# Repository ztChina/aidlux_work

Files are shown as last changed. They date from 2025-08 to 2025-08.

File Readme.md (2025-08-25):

## 目录
* [项目介绍](#项目介绍)
* [系统架构](#系统架构)
* [环境及依赖配置](#环境及依赖配置)
* [硬件配置](#硬件配置)
* [运行](#运行)

## 项目介绍
- 本项目基于思岚 RPLIDAR A1 激光雷达，使用 Gmapping 进行 2D SLAM 建图，并通过 ROS Navigation Stack 实现全局/局部规划与 AMCL 粒子滤波定位的自主导航。项目包含：
    - 雷达驱动与 TF 配置
    - Gmapping 参数优化与地图保存
    - AMCL 定位与导航（全局/局部路径规划）
    - YOLO 人体识别（融合视觉与雷达/里程计，支持跟随/到人）
    - 语音交互导航（语音设定目标点、启停、模式切换与状态播报）
    - 可即用的启动脚本与参数模板，帮助快速部署到实际机器人

## 系统架构


## 环境及依赖配置
- ROS相关环境配置及依赖安装见[相关文档](https://github.com/ztChina/aidlux_work/blob/main/ros_navigation/README.md)
- YOLO相关环境配置及依赖安装见[相关文档](https://github.com/ztChina/aidlux_work/blob/main/vision_part/README.md)
- 语音1交互相关环境配置及依赖安装见[相关文档](https://github.com/ztChina/aidlux_work/blob/main/AI_part/readme.md)
- 语音2交互功能相关环境配置及依赖安装见[相关文档](https://github.com/ztChina/aidlux_work/tree/main/Dialog-models-and-plugins)
- STM32相关环境配置与原理图见[相关文档](https://github.com/ztChina/aidlux_work/blob/main/%E5%B5%8C%E5%85%A5%E5%BC%8F%E9%83%A8%E5%88%86/readme.md)

## 硬件配置


[可查看 xlsx文件](https://github.com/ztChina/aidlux_work/raw/main/硬件清单.xlsx)

## 运行
### [ROS部分运行示例](https://github.com/ztChina/aidlux_work/blob/main/ros_navigation/README.md#%E5%90%AF%E5%8A%A8%E7%A4%BA%E4%BE%8B)
### [语音交互部分](https://github.com/ztChina/aidlux_work/blob/main/Dialog-models-and-plugins/README.md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)

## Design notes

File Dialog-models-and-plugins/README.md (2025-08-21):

# 目录
* [基本功能](#基本功能)
* [调试文档](#wukong语音交互调试文档)

# 基本功能
## 1.与`ROS`通信
```
pip install pyzmq
```
- `data_publisher.py`
- `ros_listener.py`

## 2.与`stm32`通信
```
pip install pyserial
```
- `get_stm32_msg.py`<br>
监听串口，一旦满足条件，则会发布到指定信息到socket本地6000端口。

## 3.功能：
### 1. `JustRun.py`：  <br>
接收跑路指令，并把消息发送给`ROS`，自动导航到指定地点。 <br>
### 2. `Water.py`： <br>
接收用户询问，返回湿度情况。
###  3. `get_stm32_msg.py`：<br>
接收`stm`串口通信，并在后台检测湿度变化，满足条件后唤醒，并输出语音，然后发消息给`ros`。
##### 3.1 `LifeCycleHandler.py`：

```python
# ...existing code...

    def onHumidityWakeup(self, text="嘴巴干了，猎杀时刻，启动！"):
        """
        湿度唤醒：只提示，不进入录音
        """
        logger.info("onHumidityWakeup")
        self._beep_hi()
        if config.get("/LED/enable", False):
            LED.wakeup()
        self._unihiker and self._unihiker.record(1, text)
        self._unihiker and self._unihiker.wakeup()
        # 直接语音播报
        self._conversation.say(text, True)

# ...existing code...
```
##### 3.2 `wukong.py`：

```python
import sys
import socket
import threading
sys.path.append("/root/.wukong/custom")
from data_publisher import DataPublisher

# ...existing code...    
    def socket_listener(self, host='127.0.0.1', port=6000):
        """
        监听本地 socket，接收唤醒信号
        """
        s = socket.socket(socket.AF_INET, socket.SOCK_STREAM)
        s.bind((host, port))
        s.listen(1)
        print(f"湿度唤醒监听已启动: {host}:{port}")
        while True:
            conn, addr = s.accept()
            data = conn.recv(1024).decode()
            if data == "WAKEUP":
                print("收到湿度唤醒信号，唤醒机器人")
                self.lifeCycleHandler.onHumidityWakeup()
                # time.sleep(1.5)  # 等待唤醒
                publisher = get_publisher()
                while True:
                    message = "status 找人通知：口干干，喝水水"
                    if publisher.send_message(message):
                        break
            conn.close()
# ...existing code...
```

```python
 def run(self):
        self.init()
# ...existing code...
        # 启动 socket 监听线程
        threading.Thread(target=self.socket_listener, daemon=True).start()
# ...existing code...
```

### 4. `move.py`：  <br>
接收移动指令，通过百度`UNIT`识别`方向`和`距离`，并把消息发送给`ROS`。 <br>

### 5.`AI.py`,`car_control.py`: <br>
提示词，ai根据模板生成对应代码。

# wukong语音交互调试文档

官方教程：[链接](https://wukong.hahack.com/#/README)

### 1.安装

板子系统默认3.10版本，不要`python3.10`版本，有bug，安装3.9版本

#### 1.1 下载安装激活`conda`虚拟环境

```bash
mkdir -p ~/miniconda3
wget https://repo.anaconda.com/miniconda/Miniconda3-latest-Linux-aarch64.sh -O ~/miniconda3/miniconda.sh
bash ~/miniconda3/miniconda.sh -b -u -p ~/miniconda3
rm ~/miniconda3/miniconda.sh
```

**激活虚拟环境**

```bash
source ~/miniconda3/bin/activate
#conda init --all
conda create -n py39 python=3.9
conda activate py39
```

#### 1.2 手动安装wukong

[教程](https://wukong.hahack.com/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)

```
 git clone https://ghfast.top/github.com/wzpan/wukong-robot.git
```

```
git clone  https://ghfast.top/wzpan/wukong-contrib.git contrib
```

### 2.音频配置

#### 2.1 音箱Y11配置

```
alsamixer -c 1 # 或者是1
使用方向键调节音量
```



```
sudo -i
```

查看卡号

```
arecord -l
```

[配置 .asoundrc](https://wukong.hahack.com/#/run?id=配置-asoundrc)

首先创建 `~/.asoundrc` ：

```
vim ~/.asoundrc
```

```
pcm.!default {
        type plug slave {
                pcm "hw:0,0"
        }
}

ctl.!default {
        type hw
        card 0
}
```

测试：

```
arecord test.wav
aplay test.wav
```

### 3.配置文件

第一次运行之后，创建配置文件，打开文件

```
vim ~/.wukong/config.yml
```

```
:set fileencoding=utf-8
:w
```

#### 3.1 配置唤醒

使用`snowboy`

环境嘈杂度：35

录音：5

#### 3.2 配置ASR

使用本地模型：`fun-asr`

模型下载：[链接](https://modelscope.cn/models/iic/speech_paraformer-large_asr_nat-zh-cn-16k-common-vocab8404-pytorch/files)

```
funasr-export ++model=paraformer ++quantize=true ++device=cpu
```

```
from funasr import AutoModel

model = AutoModel(model="paraformer", device="cpu")

res = model.export(quantize=True)
```

```
/root/.cache/modelscope/hub/models/iic/speech_paraformer-large_asr_nat-zh-cn-16k-common-vocab8404-pytorch
```

#### 3.2 配置NLU

使用`open-ai`

GPT免费api-key

https://github.com/chatanywhere/GPT_API_free?tab=readme-ov-file#%E5%A6%82%E4%BD%95%E4%BD%BF%E7%94%A8

api_key:

```
xxxxxxxxxxxxxxxxxxxxxxxxxxxx
```

api_base:

```
https://api.chatanywhere.tech/v1/chat/
```

### 运行

```
sudo -i
conda activate py39
vim /root/.wukong/custom/data_publisher.py
python /opt/wukong-robot/wukong.py
```

### 关闭

```
Ctrl+\
```



```
sudo netstat -tulnp | grep LISTEN
sudo kill -9 <PID>  # 端口5001 对应的
```

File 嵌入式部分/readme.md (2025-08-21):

## 本项目嵌入式部分完成了串口的标准库重定向以及Micro库的重定向
可以参考这篇文档https://blog.csdn.net/struggle_success/article/details/134621868



## 本项目全部采用STM32CubeMX现代化HAL库开发
要启动系统时钟和总线，对时钟进行分频，讲.h和.c文件分开存放，便于代码的维护。

## STM32F407ZGT6实现HX711裸机移植
本设计中需要在运行时连接传感器，不然会阻塞运行。

## STM32F407ZGT6实现DHT11移植
注意使用定时器实现us级延时

## STM32F407ZGT6实现LCD V3屏幕移植
开启FSMC使用，注意使用对应的接口。该屏幕只支持FSMC配置。

## motor文件夹实现STM32F407ZGT6裸机编码器测速电机PWM驱动
体会理论与实际的差距，PWM输出理论控制，编码器测得实际值。

## sensor_test_final实现所有传感器的整合以及驱动
体会多传感器耦合协作设计

## PCB原理图



## PCB图



## PCB实物

d81dec2f7c321c4d4febcafe73a2cb19_720

## PCB三维图



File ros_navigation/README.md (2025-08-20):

# 使用`nav+gmap`实现两轮差速`ROS`小车的建图与导航并实现人体识别和语音交互导航
本项目基于思岚-A1激光雷达，使用 `Gmapping` 进行`SLAM`建图，并通过 `ROS Navigation Stack` 实现自主导航。包含雷达驱动配置、`Gmapping`参数优化、地图保存及导航（全局/局部路径规划、`AMCL`定位）的全部内容。适用于机器人自主探索、室内导航等场景，提供详细的参数配置指南和启动脚本，帮助快速部署。
## 主要功能
- `Gmapping`建图
- `Navigation`路径规划与避障

## 依赖安装
- `Joint_state_publisher`和`robot_state_publisher`的安装
- 这两个包是 `ROS` 中用于机器人模型（`URDF`）状态发布和 `TF` 变换的重要工具，通常用于导航、仿真和可视化（如 `RViz`）。若未安装以上依赖包直接运行程序则机器人模型将无法加载到`RVIZ`中并且建图功能也会无法使用
- 使用`apt`进行安装
```python
#更新软件包列表
sudo apt update

#安装 joint_state_publisher（用于发布关节状态）
sudo apt install ros-<distro>-joint-state-publisher

#安装 robot_state_publisher
sudo apt install ros-<distro>-robot-state-publisher

#注意：将 <distro> 替换为你的 ROS 版本（如 humble 或 melodic）

#安装 GUI 版本（可选，提供关节控制滑块,可在rviz中控制关节旋转）
sudo apt install ros-<distro>-joint-state-publisher-gui

```
-通过以下命令验证是否安装成功：
```python
# 检查 robot_state_publisher
rosrun robot_state_publisher robot_state_publisher --help

# 检查 joint_state_publisher
rosrun joint_state_publisher joint_state_publisher --help
```
如果没有报错，说明安装成功。

- `Navigation`的安装
- `Navigation`是一个开源的机器人导航框架，他的功能是让机器人安全地从`A`点移动到`B`点。路径规划、避障和自主脱困等动能是`Navigation`所具备的基本能力
-使用`apt`安装
```python
# 更新软件包列表
sudo apt update

# 完整安装 Navigation Stack
sudo apt install ros-<distro>-navigation

# 或最小化安装核心组件
sudo apt install ros-<distro>-move-base ros-<distro>-amcl ros-<distro>-map-server

#注意：将 <distro> 替换为你的 ROS 版本（如 humble 或 melodic）。
```
验证安装：
```python
# 检查 move_base
rosrun move_base move_base --help

# 检查 AMCL
rosrun amcl amcl --help

# 检查 map_server
rosrun map_server map_server --help

```
- `Gmapping`建图依赖包及雷达驱动都已包含在项目中。

## 启动示例
### 启动建图功能
- 首先启动`driver_node`下的`driver_node.py`文件,具体命令如下：
```python
# 在chapt目录下完成编译工作
colcon build
source install/setup.bash

# 启动driver_node.py
ros2 run driver_node driver_node.py
```
`driver_node.py`文件内包括对`stm32`端发送的底盘速度信息，通过计算将速度信息转化为里程计数据并发布到`odom`话题并将`odom`与`base_link`的节点连接起来，并、启动`urdf`文件发布机器人从`base_link`到`laser`的`TF`树、启动`stm32`端接收`ROS`端发送的速度命令功能。
- 其次启动`rplidar_ros`下的`test_gmapping.launch.py`文件，并在终端中启动`rviz`
```python
#启动test_gmapping.launch.py
ros2 launch rplidar_ros test_gmapping.launch .py

#新开一个终端，启动rviz
rviz2
```
`gampping`产生的地图会通过`/map`话题进行发布，所以可以通过`rviz`订阅话题进行显示，在`rviz`中将`Fixed Frame`修改为`map`，接着点击`add`在话题中添加`/map`话题

再重开一个终端，启动键盘控制节点，控制小车移动完成完整地图建立
```python
#键盘控制节点
ros2 run teleop_twist_keyboard teleop_twist_keyboard
```
在建图操作完成后，输入以下命令保存地图，或者在启动`test_gampping.launch.py`文件前解开该文件内底部的`map_save_launch`代码注释，这将启动地图自动保存功能，时间间隔是30s（使用前确保该代码内的地图保存路径正确）
```python
#安装地图服务
sudo apt install ros-$ROS_DISTRO-nav2-map-server 
#保存地图（默认保存在home目录下）
ros2 run nav_map_server map_saver_cli -f room
```
注意，在进行建图时，请确保整个机器人的`tf`树与`map``odom`的正确连接
### 启动导航功能
- 首先和启动建图第一步一样，启动`driver_node.py`文件，启动小车的底盘控制
- 完成以上操作后，启动`rplidar_ros`文件夹下的`prepare_for_nav.launch.py`文件，启动导航所需要的依赖项
```python
ros2 launch rplidar_ros prepare_for_nav.launch.py
```
- 最后，启动`daohang`文件夹下的`nav.launch.py`文件
```python
ros2 launch daohang nav.launch.py
#完成nav.launch.py文件的启动后，再开一个新的终端，启动Rviz
```
完成以上操作后可以看见`rviz`中已经正确加载我们的地图，但是此时`rviz`中会出现`tf`相关的错误，这是因为此时还没由设定机器人的初始位置，在`rviz`的工具栏中选择`2D Pose Estimate`单击机器人在地图中目前所在的大概位置，拖动鼠标调整机器人朝向，若觉得不够准确可以多次调整，然后使用`Nav2 Goal`给定目标点与朝向，让机器人自主进行导航。

### 启动语音交互导航
- 在完成以上启动导航功能的基础下，启动`duodian`文件下的`yvying_jiaohu_daohang.py`文件用于初始化导航位置，其次启动`ros_listener.py`文件用于监听语音大模型发送的导航命令
```python
#启动yvying_jiaohu_daohang文件
ros2 run duodian yvying_jiaohu_daohang

#启动语音监听节点(启动前请确认语音大模型与机器人处于同一网络下，并修改文件内顶端的ip地址)
ros2 run duodian ros_listener

#可启动shiyan文件用于测试导航节点是否正确（启动前请在文件内解开需要的代码注释或添加需要的测试代码）
ros2 run duodian shiyan
```
完成以上操作后，请根据语音大模型模块的介绍通过语音交互发布导航命令

### 启动YOLO人体识别导航
- 和启动语音交互功能一样，在启动导航功能的基础上，启动`duodian`文件下的`renti_shibi_daohang.py`文件
```python
ros2 run duodian renti_shibi_daohang
```
启动以上文件后，当机器人识别到人后便会自动向特定话题发布信息，`ros`端接收到信息后便会前往对方身边。

# 结语
以上文件只包括了`ros`控制方面的代码未包括语音模块，`YOLO`模块，`stm32`端的底盘控制代码，`stm32`端只需完成底盘速度的发布与接收功能即可。

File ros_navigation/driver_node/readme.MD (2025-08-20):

# 驱动节点包 #

## 文件介绍 ##

driver_node与下位机通信，fake_stm32模拟串口通信，使用虚拟串口测试
创建虚拟串口对
driver_node使用/dev/pts/X ，另外的fake_stm32 使用/dev/pts/Y
sudo apt install socat
socat -d -d pty,raw,echo=0 pty,raw,echo=0

接收'cmd_vel'，向下位机发布速度控制命令

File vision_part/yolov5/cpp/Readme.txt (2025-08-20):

Use the steps Description：

1.  sudo apt update
    sudo apt-get install cmake -y

# Our sample program in [/usr/local/share/aidlite/examples/] directory.
# We recommend that you copy the sample program directory to your own working directory.
2.  mkdir -p /home/aidlux/your_work_dir/ && cp -r /usr/local/share/aidlite/examples/ /home/aidlux/your_work_dir/
    cd /home/aidlux/your_work_dir/examples/aidlite_qnn/cpp/

# If you do not want to copy the sample program, then next few steps require Sudo permissions
3.  mkdir -p build && cd build
4.  cmake ..
5.  make 

# Run the resulting executable program
6.  /xxx.exe

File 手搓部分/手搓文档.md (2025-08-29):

# 智能花盆---植物陪伴机器人

# 目录

[TOC]

# 项目介绍

		该**智能花盆项目**，也称**植物陪伴机器人项目**，是基于 **AidLux 平台** 的一个实践型开发与实验仓库，使用阿加犀公司的开发板[犀牛派A6490PM1](https://e.tb.cn/h.huDp7wvc6znr8JO?tk=9Nrz4PhG3og )，主要围绕底盘控制、MCU开发、机器人导航、环境建图、语音交互以及多模块系统协同展开。该项目充分利用 AidLux 融合操作系统的特性，拥有在 Android 设备上运行完整 Linux 环境的能力，实现 Android 与 Linux 的无缝融合，而不是简单的双系统切换，并借助丰富的 AI 工具链与外设接口支持，为机器人应用的快速开发和部署提供了良好环境。

		在功能层面，项目重点实现了ROS 导航与建图、 AI 语音交互、自动浇水和缺水寻人功能。通过引入 SLAM（同步定位与建图）算法与导航框架，机器人能够在未知环境中完成**地图构建**与自主定位，从而支持路径规划和**目标点导航**，并嵌入有动态障碍物识别功能，从而提升机器人在复杂环境下的导航安全性；作为陪伴机器人，通过本地部署的LLM模型，配合前后端的音频处理方法和模型，能和用户建立起有效的情感连接，同时使用 AidLux 平台迅速部署本地植物知识库，创建一个**掌握植物知识的聊天机器人**；为了更智能地管理植物，能让用户在种植一株植物，拥有一个陪伴聊天机器人的同时， 减少用户浇水次数，降低用户对植物的养护时间，我们使用温湿度传感器对环境进行实时监测，实现花盆的**自动浇水**，并且当机器人识别到备用水不足时，开启**人体检测功能**，得到人物坐标后导航到达人物附近并询问加水。

		技术栈方面，项目覆盖了 **MCU嵌入式开发、Linux嵌入式开发、SLAM、NAV、ROS2 框架、机器视觉模型、大语言模型** 等内容，结合 AidLux 平台内置的开发环境，形成了一个软硬件一体化的研发生态。底盘使用STM32F407ZGT6作为控制板，基于FreeRTOS系统实现多传感器数据采集、自动浇水GPIO控制、USART与上位机通信、电机PID控制等多个任务，保证数据的实时性和各种功能的多线程运行；上位机A6490PM1使用ubuntu22操作系统，实现**基于 Transducer 的流式语音检测**，并通过**关键词检测策略**实现在线 KWS 功能、**基于WeNet模型**的ASR(声音转文字)、**基于WeTTS模型**的TTS(文字转语音)和**基于Qwen2.5-0.5B-Instruct_1-Q8模型**的文字交互功能，并对输入输出音频进行算法上的处理，以保证整体语音交流的顺畅的准确度；建图和导航的功能实现是**基于开源的gmapping算法**和名为**Navigation**的一个开源导航框架；最终，基于**ROS2框架**，将所有功能模块打包封装为软件包，并将各个**模块的桥接层功能实现**在一个中心控制软件包，以实现整体的初始化和工作调度。

[项目github链接](https://github.com/ztChina/aidlux_work)

# PC端软件下载

## vscode

下载链接：([Documentation for Visual Studio Code](https://code.visualstudio.com/docs/?dv=win64user))

## adb工具及其它刷机工具

软件下载链接： [软件工具安装包下载链接](https://file.aidlux.com/files?folder_id=ec5bf3bf)

#### USB驱动安装

- 解压USB_Driver_qud.win.1.1_installer_10061.1.zip文件。
- 解压后，双击setup.exe程序，等待跳出Qualcomm USB Drivers 安装界面，根据提示点击 next 即可。

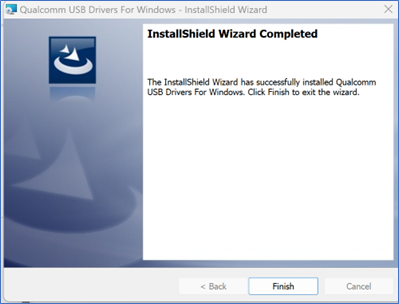
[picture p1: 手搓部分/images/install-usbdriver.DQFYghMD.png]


#### ADB工具安装

##### 1、解压platform-tool.zip

- 将platform-tools.zip文件解压到D盘。

##### 2、配置adb环境变量

- 复制解压后的platform-tools路径。

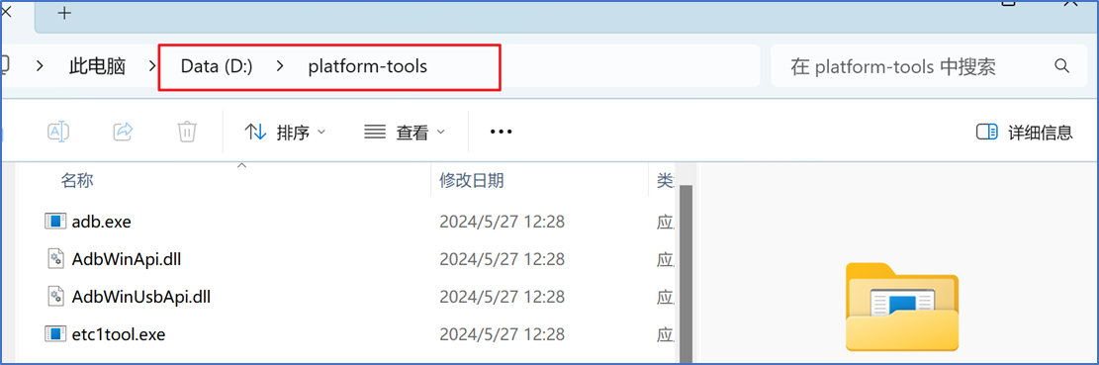
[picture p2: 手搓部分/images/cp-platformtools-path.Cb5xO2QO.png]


- 鼠标右键点击此"电脑-属性"。

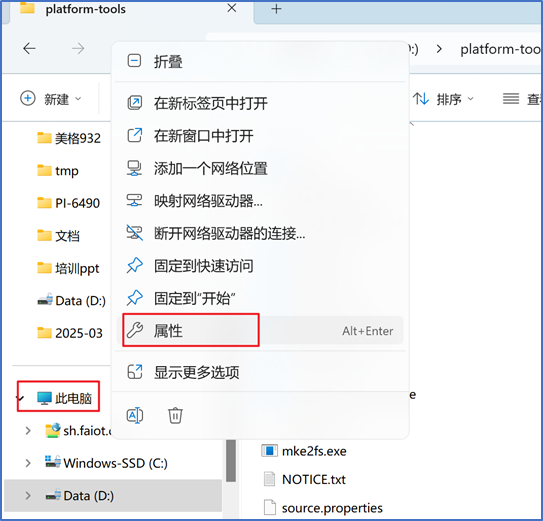
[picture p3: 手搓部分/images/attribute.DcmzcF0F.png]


- 在弹出的设置窗口，点击"高级系统设置"。

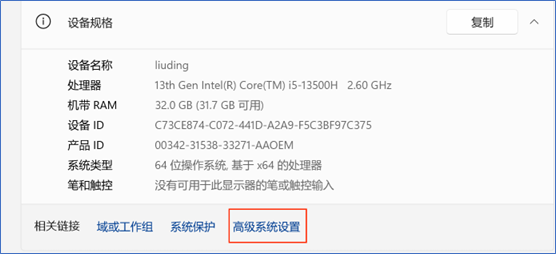
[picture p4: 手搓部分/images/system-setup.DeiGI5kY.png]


- 在弹出的系统属性窗口-高级页，点击"环境变量"。

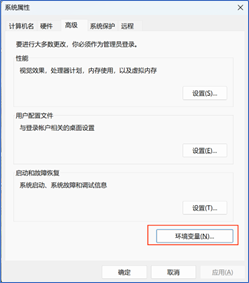
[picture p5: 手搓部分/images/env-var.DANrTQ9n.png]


- 在弹出的环境变量窗口中，选中"系统变量"栏的Path变量，点击下方的"编辑"。

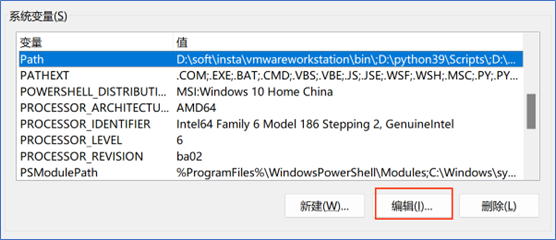
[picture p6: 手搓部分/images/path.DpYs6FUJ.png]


- 在弹出的编辑环境变量窗口中，点击"新建"，并添加前面复制的platform-tools路径。

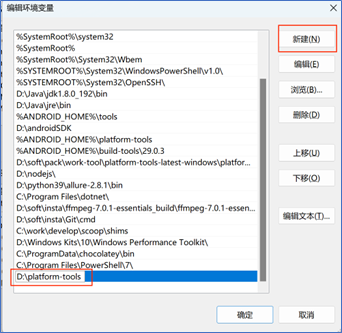
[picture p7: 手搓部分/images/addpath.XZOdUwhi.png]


- 依次点击"确认"来保存设置的变量，并退出。

##### 3、 验证adb环境配置是否可用

- 打开cmd窗口，输入adb，查看回显中存在[配置adb环境变量](#2、配置adb环境变量)章节复制的adb安装路径。

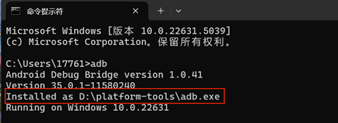
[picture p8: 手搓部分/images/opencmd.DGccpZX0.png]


#### 刷机工具安装

- 解压QPST_2.7.496.zip文件到当前文件夹。
- 进入到解压后的QPST_2.7.496目录，双击QPST.2.7.496.1.exe程序，进行安装。

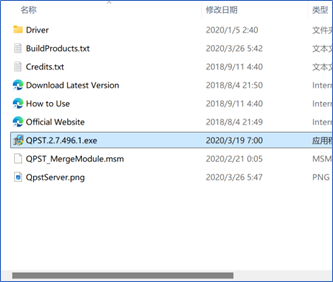
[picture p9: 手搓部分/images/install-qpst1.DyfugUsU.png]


- 根据提示，一直点击"next"即可完成安装。
- 安装完成后的默认路径：C:\Program Files (x86)\Qualcomm\QPST\bin 。
- 可进入该目录，将QFIL.exe程序发送到桌面。

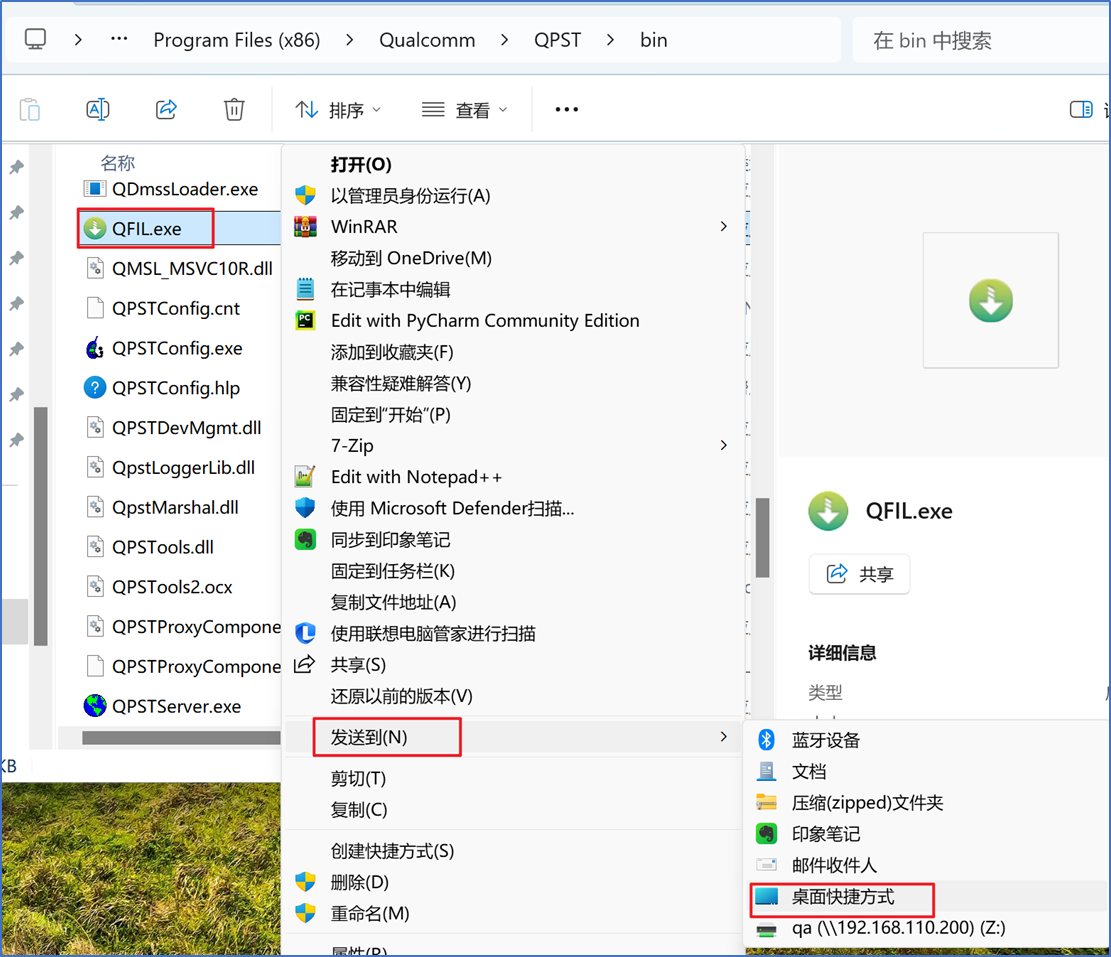
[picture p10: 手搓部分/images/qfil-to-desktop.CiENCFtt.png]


- 桌面图标如下。

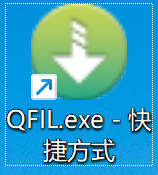
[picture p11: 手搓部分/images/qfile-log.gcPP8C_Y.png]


#### 拷屏工具安装

提示

拷屏工具版本会不定时更新，请参考QtScrcpy-win-x64-v2.2.1版本进行安装。

- 解压QtScrcpy-win-x64-v2.2.1.zip到任意目录
- 进入到解压后的目录，找到QtScrcpy.exe文件

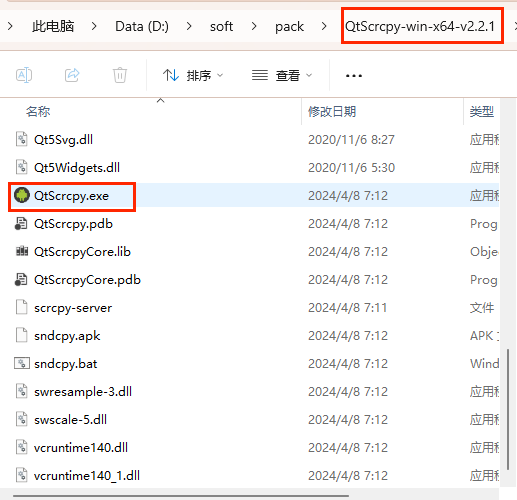
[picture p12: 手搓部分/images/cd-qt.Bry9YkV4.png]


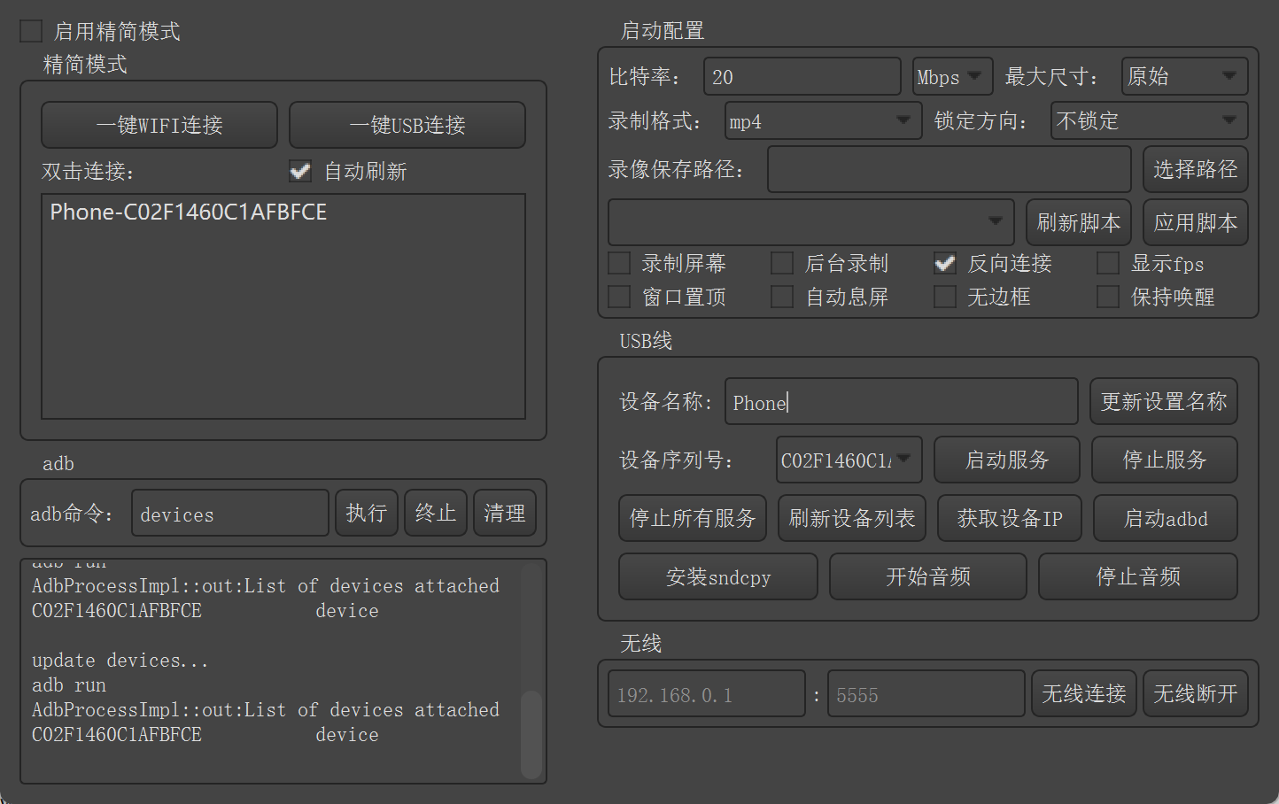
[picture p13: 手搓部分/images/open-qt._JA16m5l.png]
- 双击该可执行程序打开，当用Type-C线缆连接后，双击设备名则可以开始拷屏。
- 为方便下次使用，可以将该可执行程序发送到桌面快捷方式。

## Keil uvision5 MDK

`Keil uvision5 MDK`安装包：https://pan.baidu.com/s/5tx8NAAUpELTvOPtTsQl-Vg

`Keil uvision5 MDK`安装流程：https://mp.weixin.qq.com/s/63JQncEWlw8oFK8lX9IV4A

## STM32CubeMX

`STM32CubeMX`安装包：[【正点原子STM32】STM32CubeMX入门(搭建Java运行环境、STM32CubeMX安装、新建STM32CubeMX工程步骤、STM32CubeMX用户使用手册)-CSDN博客](https://blog.csdn.net/m0_62140641/article/details/135683008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)

`STM32CubeMX`安装流程：[【正点原子STM32】STM32CubeMX入门(搭建Java运行环境、STM32CubeMX安装、新建STM32CubeMX工程步骤、STM32CubeMX用户使用手册)-CSDN博客](https://blog.csdn.net/m0_62140641/article/details/135683008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)

`STM32CubeMX`使用教程：[【正点原子STM32】STM32CubeMX入门(搭建Java运行环境、STM32CubeMX安装、新建STM32CubeMX工程步骤、STM32CubeMX用户使用手册)-CSDN博客](https://blog.csdn.net/m0_62140641/article/details/135683008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)

## SSCOM串口通讯助手

`SSCOM`安装包：[百度网盘 请输入提取码](https://pan.baidu.com/share/init?surl=6xUcdI4pRaaCjPcHwjgPQA&pwd=mc4x)

`SSCOM`安装流程：解压后直接双击打开使用

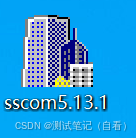
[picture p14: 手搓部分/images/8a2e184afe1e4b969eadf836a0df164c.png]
在这里插入图片描述


`SSCOM`使用教程：[【工具】SSCOM V5.13.1串口工具-基础使用（图文详情）-CSDN博客](https://blog.csdn.net/qq_41539778/article/details/135965840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)

## PCtoLCD2022（OLED屏显）

`PCtoLCD2002`使用教程：[LCD / OLED显示汉字，取模软件PCtoLCD2002完美版-CSDN博客](https://blog.csdn.net/luyibing2017/article/details/125317599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)

## STM32F407芯片包下载

`STM32F407`芯片包下载：[STM32F407固件库的下载与安装_stm32f407固件库下载-CSDN博客](https://blog.csdn.net/rain_turns_shade/article/details/147116903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芯片包下载&spm=1018.2226.3001.4187)

# 刷机部分

## 1、先安装win端工具 软件

链接：[AidLux](https://file.aidlux.com/files?folder_id=ec5bf3bf)

参考[安装方法](#adb工具及其它刷机工具)

## 2、再按照[美格6490刷机](.\code_part\test_code\刷机部分\美格(MC932)-QC6490-刷机流程.doc)流程刷机

其中使用到的固件版本文件[(A6490BM1-A14.zip)](.\code_part\test_code\刷机部分\)

## 3、ADB上传aidlux的SDK

type-c 连接板卡和笔记本，PC终端使用 `adb devices` 命令确定连接上开发板，打开[apk包](.\code_part\test_code\刷机部分\aidlux_2.0.1.1854_enterprise_qc6490_lu2204_robot_20250701-145237)后，直接点击install 就好，等到上传到100%

## 4、打开Qt拷屏桌面，打开一次桌面刷新

等到Qt桌面刷新到100%结束，再进行操作

## 5、进入web端，安装ros2和Ubuntu Desktop

参考[开发板安装软件](#7、开发板ros2及各种软件下载)

## 6、在普通用户和root的.bashrc文件中加入

```shell
# my config for work
# 这一句是将终端前面的提示词变为绿色
export PS1='\[\e[01;32m\]\u@\h:\w\$\[\e[00m\]'
# 下面两句是加载ros环境
source /opt/ros/humble/setup.bash
source /home/aidlux/[你的ros工作空间]/install/setup.bash
```

## 7、MC932-OTA版本升级操作：

	1、有时需要更新板卡中的固件，需要做升级操作如下，

	2、个人终端和板卡type-c连接

	3、将OTA包通过adb push 命令上传到sdcard/update.zip

```shell
adb push D:\出货相关\MC932-融合系统\固件
ROM\SNM932-A14_EQ000_2774.867AEABBCE.C9B7386.A8D9AEA_250630_100_V01_T06_ota.zip sdcard/update.zip
```

	 3、 push 成功后，执行如下命令，进行OTA升级

```shell
adb shell
ota
```

	某些版本升级后检查：

	1、执行如下命令，检查配置文件中是否新增eth0、eth1和wlan0 mac 地址，预期配置文件中有mac 地址回显

```shell
adb shell
cat /sys/devices/virtual/ssignrwtest/mytest_device/iopartition
```

2、执行如下命令，检查wlan0 的mac 地址与上述配置文件中记录的mac地址是否一致。预期ifconfig 命令实际查询额mac 地址与配置文件中的mac 地址一致。

```shell
ifconfig
```

# 常用操作

## 1、vscode使用SSH连接

vscode插件下载

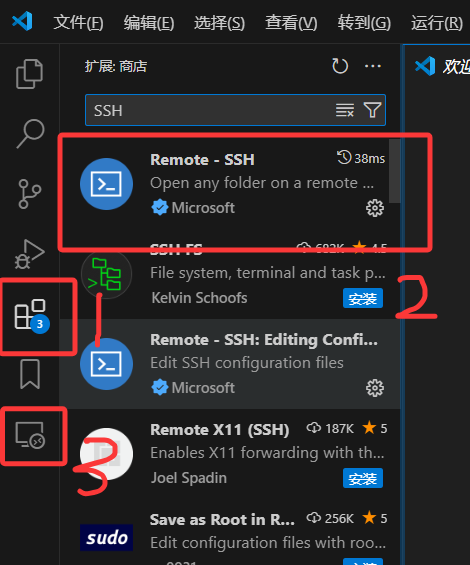
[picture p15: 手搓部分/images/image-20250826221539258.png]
	

选择ssh配置文件

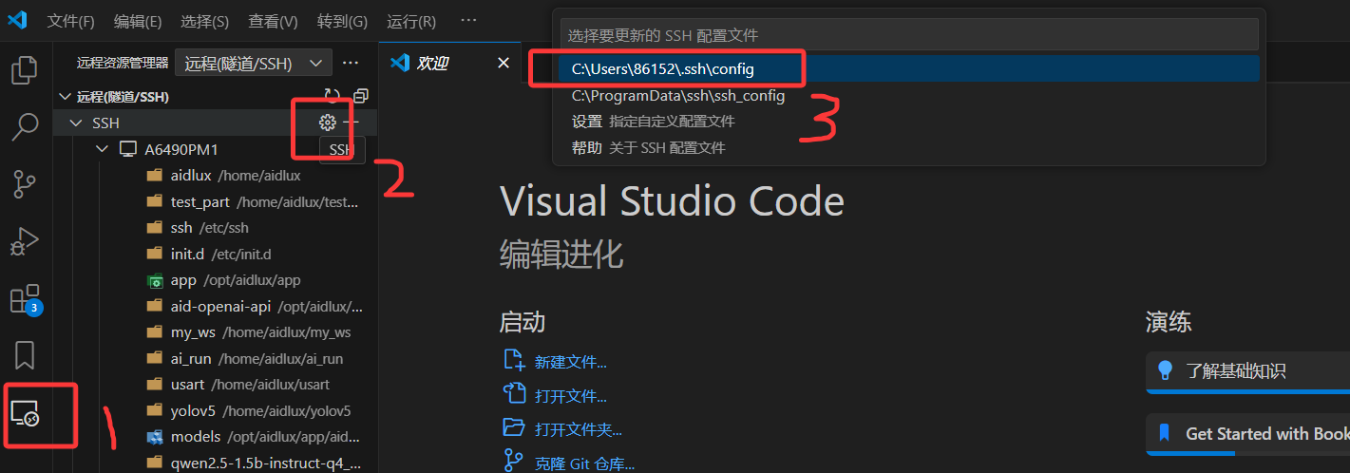
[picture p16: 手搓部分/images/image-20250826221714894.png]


按照下述格式书写添加SSH连接

```python
Host [name]
 HostName [IP]
 User [USER_NAME]
```

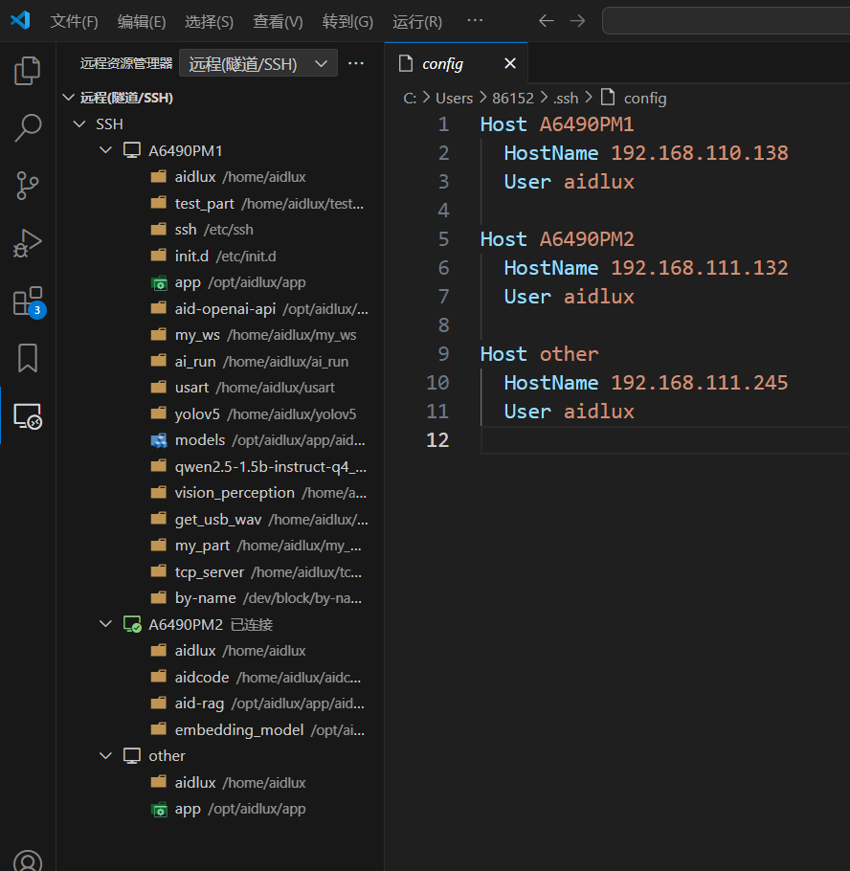
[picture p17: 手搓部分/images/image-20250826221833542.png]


选择进入对象

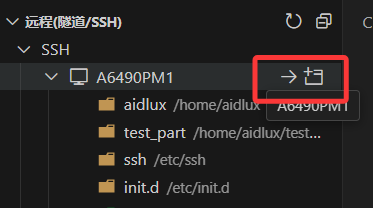
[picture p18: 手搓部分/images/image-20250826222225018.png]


然后输入密码并选择文件夹即可

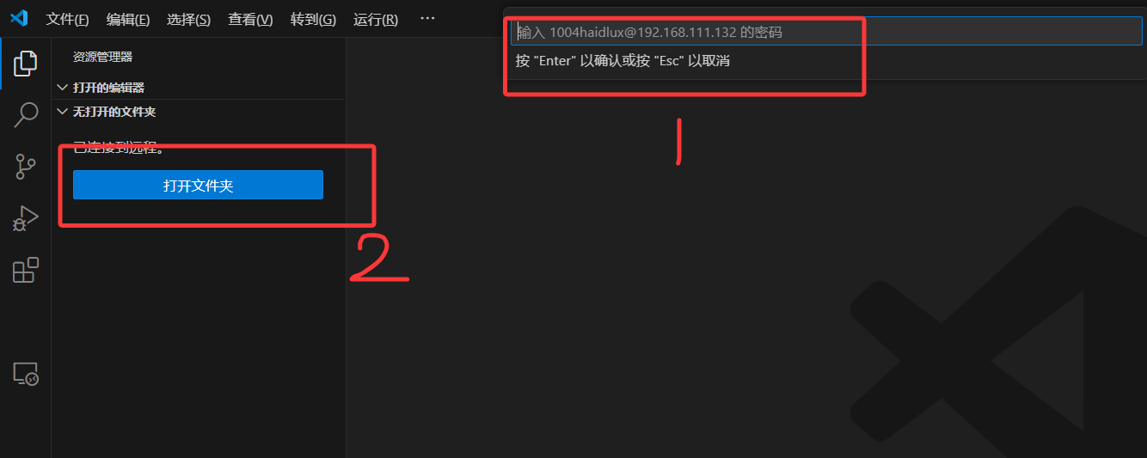
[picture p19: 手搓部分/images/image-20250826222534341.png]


## 2、打开windows终端

右键开始，选择`终端`即可，可以将其固定在任务栏

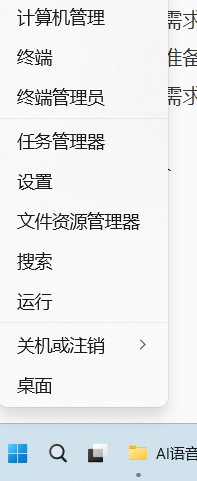
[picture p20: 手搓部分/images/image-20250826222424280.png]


## 3、打开web端界面

在浏览器中使用IP:8000端口打开开发板的web服务，输入密码aidlux

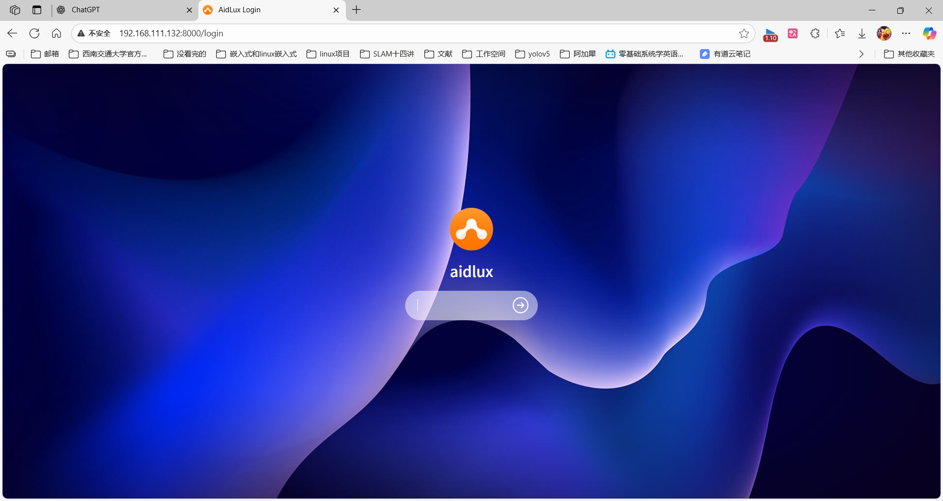
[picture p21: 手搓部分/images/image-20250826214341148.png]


## 4、打开ubuntu桌面

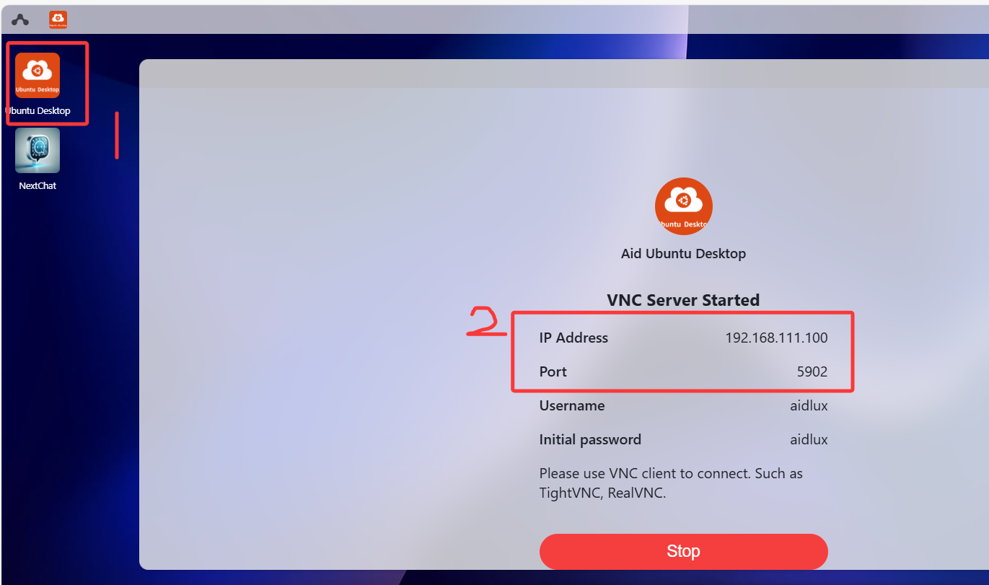
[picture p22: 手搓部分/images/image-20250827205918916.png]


IP和端口5902，之后可以使用VNC连接

## 5、VNC进入ubuntu桌面

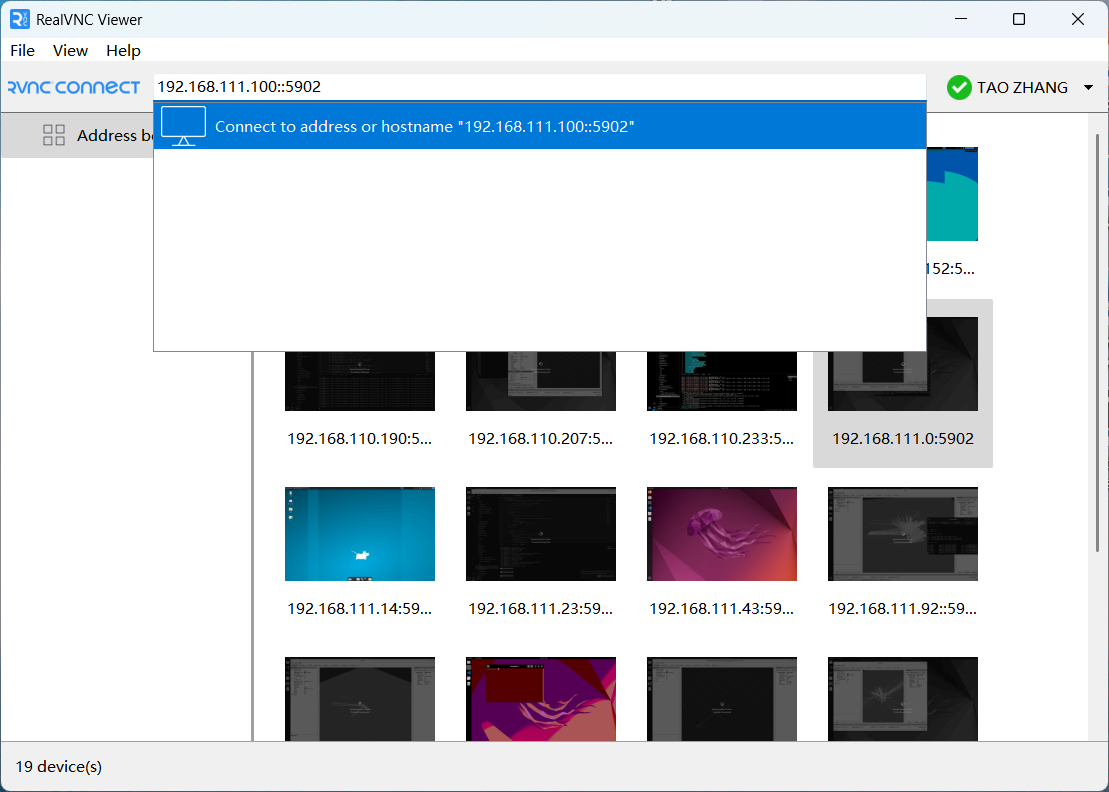
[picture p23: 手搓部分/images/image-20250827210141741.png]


## 6、windows终端使用adb工具获取开发板IP

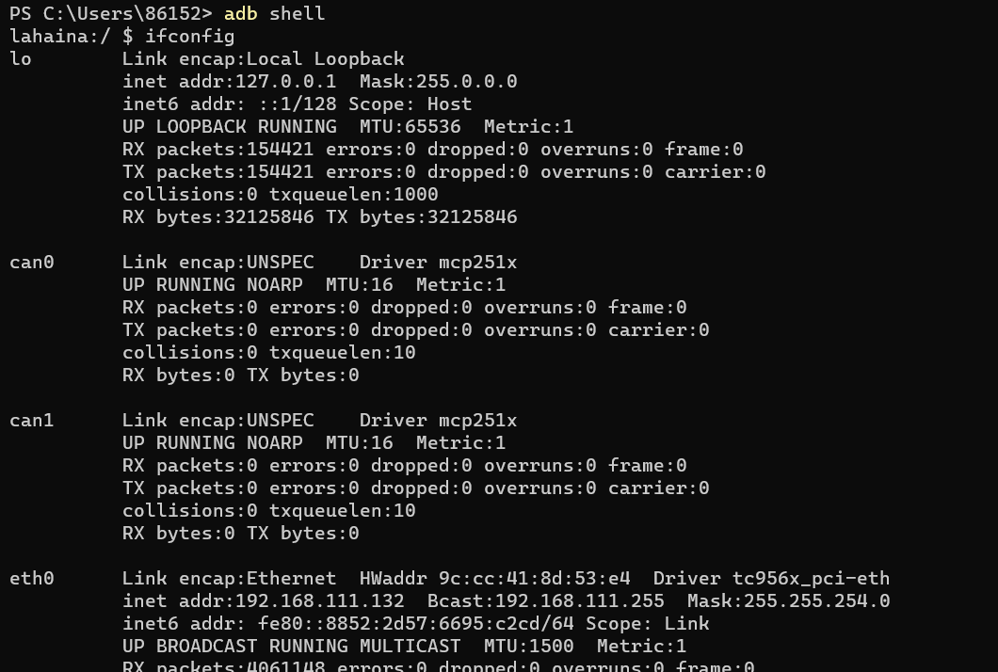
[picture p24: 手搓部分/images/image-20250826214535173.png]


## 7、开发板ros2及各种软件下载

1. 浏览器访问板卡eth0 网口IP:8000 端口，进入aidlux 桌面

2. 打开App Store后，找到Ubuntu Desktop 应用

   

3. 点击右上角安装，等待安装完成即可

   

   4. ROS2-Humble、Gazebo、Moveit2 下载步骤同上

# bom（物料清单）

| 序号 | 名称 | 型号/规格 | 数量 | 单位 | 备注 |
| ---- | --- | --- | ---- | ---- | :---: |
| 1 | 开发板 | 阿加犀-犀牛派A6490PM1 | 1 | 块 | 主控板 |
| 2 | 单片机 | STM32F407 | 1 | 块 |  下位机控制  |
| 3 | 稳压板 | DC3.3V DC5V DC可调 | 1 | 个 |  元器件供电  |
| 4 | TB6612电机驱动板 | AT8236双路直流电机带稳压驱动模块 | 1 | 个 | |
| 5 | 电机 | MG513直流减速电机马达带GMR霍尔编码器 | 2 | 个 | |
| 6 | 继电器 | 1路3.3V（红板支持高低电平触发） | 1 | 个 | 控制水泵 |
| 7 | 微型蠕动泵 | 0.1-2ml/min）3V固定流量 | 1 | 个 | |
| 8 | 压力传感器 | HX711 | 1 | 个 | 压力监测水位 |
| 9 | 温度传感器 | DS18B20防水型温度传感器 | 1 | 个 | |
| 10 | 湿度传感器 | DFRobot电容式土壤湿度传感器 | 1 | 个 | |
| 11 | 激光雷达 | RPLIDAR A1高速版 | 1 | 个 | |
| 12 | USB摄像头 | F1080P_3.5mm90度（无畸变） | 1 | 个 | |
| 13 | USB麦克风音箱一体机 | G-MARK | 1 | 个 | |
| 14 | mini下载器 | mini-HADAP | 1 | 个 |  单片机烧录  |
| 15 | USB转TTL模块 | CH340 USB转TTL | 1 | 个 | 打印调试 |
| 16 | 杜邦线 | 母对母 公对公 公对母 | \ | \ | |
| 17 | 12V10A电源分接线 | DC5.5一分三电源线 | 1 | 个 | |
| 18 | 电池 | 12V 5100mAh E351S | 1 | 个 | |
| 19 | 万向轮 | 1英寸 万向轮金属牛眼轮 | 1 | 个 | |
| 20 | 车轮 | 65mm橡胶车轮 | 2 | 个 | |
| 21 | 国产BPT管 | 1.5mm*2.5mm | 1 | 个 | 水管 |

点击查看[物料清单表(.xlsx)](.\物料明细.xlsx)

# 传感器配置和测试

## USB摄像头

### 1 准备

- 犀牛派A1
- 在AidLux-ubuntu22.04上预装ubuntu desktop、ros2、rviz2 具体安装方法可参照[开发板ros2及各种软件下载](#7、开发板ros2及各种软件下载)
- 复制[USB摄像头软件驱动包](.\code_part\src\camera_start_python)到你的工作空间

执行以下命令编译软件包

```shell
aidlux@aidlux:~$ cd my_ws/
aidlux@aidlux:~/my_ws$ colcon build
Starting >>> camera_start_python
Finished <<< camera_start_python [2.69s]          

Summary: 1 package finished [2.97s]
aidlux@aidlux:~/my_ws$ 
```



### 2 硬件连接

将USB摄像头连接到犀牛派的USB接口

### 3 测试

- 连接好后，通过如下命令启动相机驱动

```shell
aidlux@aidlux:~/my_ws$ source install/setup.bash 
aidlux@aidlux:~/my_ws$ ros2 run camera_start_python cam_pub 
```

- 打开终端并输入:rviz2

```shell
rviz2
```



- 在rviz2中验证打开相机图像画面

点击左下角Add按钮



在弹框中点击By topic



双击打开/camera节点下的image，观察到左下角的image弹框出现相机拍摄的画面





## USB麦克风音箱一体机

我们使用的是一个USB接口可以实现音箱和麦克风两种功能的一体化设备

连接好USB之后，设备音麦设备上显示亮灯，上为音箱，下为麦，亮蓝为打开，灭或者红光为关闭



### 1 准备

- 犀牛派A1
- USB麦克风音箱一体机

### 2 硬件连接

将USB头连接到犀牛派的USB接口

### 3 测试

#### 3.1 录音测试

- 列出所有录音设备

```
sudo arecord -l
```



找到USB Audio，读取到该设备的声卡编号即card x(x即为声卡编号)，读取到该声卡下的设备编号即device y(y即为子设备编号)，设备标识格式：hw:X,Y（X 是声卡编号，Y 是子设备编号）。当前示例读取出的设备标识为： hw:1,0

- 列出设备所支持的各项参数

```
sudo arecord -D hw:1,0 --dump-hw-params
```



注意如下几个参数：

FORMAT：设备支持的采样格式。目前支持的格式为：S16_LE

CHANNELS：表明设备支持的声道数量范围。当前声道数量为：2

RATE：显示设备支持的采样率范围，单位为HZ。目前支持的采样率为：44100 和 48000 (推荐48000)

- 开始录音

注意命令中的参数，需要与上一步骤查出来的值保持一致。如-f 即采样格式， -r即采样率， -c即声道数量，-d即录音时长。

```
sudo arecord -D hw:1,0 -f S16_LE -r 48000 -c 2 -d 5 output.wav
```



#### 3.2 音量设置

有些音箱插上去默认音量是0或者100，这有两种方式设置：

##### 3.2.1 使用命令 ` sudo alsamixer -c [声卡编号]` 修改声量大小

终端出现如下，可以通过上下键调节



##### 3.2.2 通过硬件规则绑定

###### 1、lsusb查看设备号

```shell
	Bus 002 Device 003: ID 1235:0002 Focusrite-Novation Speedio
```

###### 2、在root下使用 aplay -l查看卡号和名称，输出

```shell
card 1: Y11 [Y11], device 0: USB Audio [USB Audio]
  Subdevices: 1/1
  Subdevice #0: subdevice #0
```

发现设备名称Y11，和Focusrite-Novation不一致，使用Y11作为识别名

###### 3、使用amixer 查看通道

```shell
root@aidlux:/home/aidlux/aidcode/test#amixer -c 1
Simple mixer control 'PCM',0
  Capabilities: pvolume pswitch pswitch-joined
  Playback channels: Front Left - Front Right
  Limits: Playback 0 - 4096
  Mono:
  Front Left: Playback 819 [20%] [3.19dB] [on]
  Front Right: Playback 819 [20%] [3.19dB] [on]
Simple mixer control 'Mic',0
  Capabilities: cvolume cswitch cswitch-joined
  Capture channels: Front Left - Front Right
  Limits: Capture 0 - 4096
  Front Left: Capture 4096 [100%] [16.00dB] [on]
  Front Right: Capture 4096 [100%] [16.00dB] [on]
```

设备唯一暴露的音量play控制项（声音输出通道）为PCM

###### 4、创建文件/usr/local/bin/set-usb-audio-volume.sh

<span style="color:red">并使用chmod +x增加执行权限，否则规则文件命令没有执行权</span>

```shell
#!/bin/bash

# 获取 Y11 声卡的卡号
card_num=$(grep -m1 'Y11' /proc/asound/cards | awk '{print $1}')

# 验证卡号存在
if [ -n "$card_num" ]; then
        echo "检测到 Y11 声卡，编号为 $card_num"
        # 设置控制项
	 	amixer -c "$card_num" sset 'PCM' 20% 2>/dev/null || \
        echo "找不到匹配的控制项，需手动设置"
else
        echo "未检测到 Y11 声卡"
fi
```

###### 5、创建 udev 规则

创建一个规则文件，比如：

```shell
vim /etc/udev/rules.d/99-usb-audio-volume.rules
```

添加如下内容（替换 `1235` 和 `0002` 为你的设备 ID）：

```shell
ACTION=="add", SUBSYSTEM=="sound", ATTRS{idVendor}=="1235", ATTRS{idProduct}=="0002", RUN+="/usr/local/bin/set-usb-audio-volume.sh"
```

> #### 说明：
>
> - `ACTION=="add"` 表示设备插入时触发
> - `SUBSYSTEM=="sound"` 针对音频设备
> - `RUN+=...` 是触发脚本

###### 6、重新加载 udev 规则

```shell
udevadm control --reload-rules
```

然后重新插入你的 USB 设备，音量应该会自动设置为你脚本中设定的值。

#### 3.3 播放测试

- 列出所有播放设备

```
sudo aplay -l
```



找到USB Audio，读取到该播放设备的声卡编号即card x(x即为声卡编号)，读取到该声卡下的设备编号即device y(y即为子设备编号)，设备标识格式：hw:X,Y（X 是声卡编号，Y 是子设备编号）。当前示例读取出的设备标识为： hw:1,0

- 列出设备所支持的各项参数

```
sudo aplay -D hw:1,0 --dump-hw-params /dev/zero
```



注意如下几个参数：

FORMAT：设备支持的采样格式。目前支持的格式为：S16_LE

RATE：显示设备支持的采样率范围，单位为HZ。目前支持的采样率为：44100 48000

- 根据以上参数值可以看到，其中播放设备的采样率与录音设备的采样率一致，都为 44100 96000。但是有些设备的播放采样率与录制采样率不一致，因此我们需要将录好的音频转换一下采样率，如转换成48000的采样率，方法如下：

- 安装转换工具

```
sudo apt update
sudo apt install sox libsox-fmt-all
```

- 开始转换

```
sudo sox output.wav -r 48000 output.wav
```

如果播放采样率与录制采样率一致可跳过上述步骤

开始播放录好的音频

注意命令中的参数，需要与上一步骤查出来的值保持一致。如-f 即采样格式， -r即采样率， -c即声道数量。

```
sudo aplay -D hw:1,0 -f S16_LE -r 48000 -c 2 output.wav
```



## 激光雷达

### 1 准备

- 犀牛派A1
- 激光雷达

### 2 硬件连接

将USB头连接到犀牛派的USB接口

### 3 测试

#### 3.1 绑定雷达端口名称

雷达选用思岚—A1，该型号的雷达驱动包及相关配置文件已经整合 [src](./code_part/src/) 到`rplidar_ros`和`slam_gmapping`文件夹下，故目前只需要绑定雷达端口名称。

```python
#打开一个终端输入以下命令，将rplidar_ros文件夹下的scrips文件复制到/etc/udev/rules中
cd ~/src/rpliar_ros/scripts
sudo cp rplidar.rules /etc/udev/rules.d/
```

使用`Type_c`线将雷达和电脑连接起来，并在以上操作的终端中输入`lsusb`查看雷达的端口号

```python
#输入以下命令用于查看雷达端口号
lsusb
```

联想截图_20250827101618

记住这个框起来的端口号,进入`/etc/udev/rules.d`目录 ，修改端口号

```python
cd /etc/udev/rules.d
sudo nano rplidar.rules
```

联想截图_20250827101948

修改后按ctrl+s保存，然后按ctrl+x退出，运行修改后的规则文件

```python
sudo udevadm trigger
sudo service udev reload
sudo service udev restart
```

重新拔插雷达串口，终端输入 `ll /dev/rplidar`

```python
`ll /dev/rplidar`
```

联想截图_20250827102125

出现以上内容则表示绑定成功，结尾不一定是0，根据插入设备的顺序而改变 若未出现以上内容，在点击其他位置，打开计算机，打开`dev`，在里面查找是否有` rplidar `文件

联想截图_20250827102315

如果出现，则表示连接成功。如果没有出现，可多次尝试拔插雷达串口。

#### 3.2 雷达测试

接下来进行雷达测试，将雷达和电脑连接上后打开雷达开关，运行`"code_part\src\rplidar_ros\launch"`下的`rplidar_a1_launhc.py`文件。

```python
ros2 launch rplidar_ros rplidar_a1_launch.py

```

另开一个终端，在终端中输入以下内容用于查看雷达数据

```python
ros2 topic echo /scan
```

联想截图_20250827103110

在启动雷达点云图文件前先结束上文中启动的查看`/scan`话题的命令，在输入`ros2 topic echo /scan`的终端中输入`Ctrl+c`命令用于停止以上命令，然后启动`view_rplidar_a1_launch.py`文件

```python
# 启动view_rplidar_a1_launch.py文件用于在rviz中查看雷达点云图
ros2 run ${view_rplidar_a1_launch.py文件所在的功能包名}view_rplidar_a1_launch.py
```

注意：`view_rplidar_a1_launch.py`为测试文件，启动前需要将该文件从`test`文件夹中移动到正式代码文件夹`src`中，该命令中的最后一项可执行文件名称需要以python功能包中的`set.up`文件内对应的可执行文件名称为主。具体操作见[链接]([重学ROS2:（5）使用功能包组织ROS中的节点[Python/C++] - 陶小桃Blog (52txr.cn)](https://www.52txr.cn/2025/packnode.html))。

完成以上操作后新开一个终端用于启动`rviz`

```python
# 启动RVIZ
rviz2
```

启动后点击坐下角的`add`选项，在新弹出的界面中选择`by topic`下滑找到`LaserScan`将他添加到`rviz`中，如果操作正确`rviz`中将会出现以下画面

联想截图_20250827104359

## MG513直流电机

### 1 准备

- 犀牛派A1
- MG513直流减速电机马达
- TB6612电机驱动板
- Windows系统电脑
- STM32F407ZGT6开发板
- mini下载器
- 杜邦新若干
- USB转串口模块

### 2 硬件连接

需要将电机与电机驱动板相连，电机驱动板与STM32F407ZGT6通过杜邦线相连，USB转串口通过杜邦线与STM32F407相连，USB接电脑，下载器通过杜邦线与STM32F407直接相连，USB接电脑，按照如下接线

电机驱动板`Input_IO`接线，从下向上

```
PWMA -> PB10
AIN2 -> PD1
AIN1 -> PD0
STBY -> PB2
BIN1 -> PD2
BIN2 -> PD3
PWMB -> PB11
```

电机驱动板`Output_IO`接线，从上向下

```
E2B -> PD13
E2A -> PD12
E1B -> PA7
E1A -> PA6
GND -> STM32的GND
```

电机驱动板与电机接线

```
排线两头分别插电机和电机驱动板上即可
```

串口转`TTL`接线

```bash
GND -> GND
TXD -> PD9
RXD -> PD8
# 以下三个串口均为供电串口，三选一接即可
VCC -> 5V/3V3
3V3 -> 3V3
5V -> 5V
```

下载器连接`STM32F407ZGT6`（为单片机供电）

```
GND -> GND
SWC -> CLK
SWD -> DIO
3V3 -> 3V3
# 第二种供电（通讯）方式
Type-c直连USB UART
```

66ab13977d24888ca1dfc7d138727c47

在这一部分，请确保$STM32F407ZGT6$通电，电机驱动板通电，接线没有短路，断路等情况，并且电机驱动板开关常开

### 3 测试

打开电机测试专用 `keil` 项目的 [test_us.uvprojx 文件](.\code_part\test_code\嵌入式部分\PID调参(电机部分)\MDK-ARM\test_us.uvprojx)

看到 `serial_command.c` 文件中 `PID` 控制部分



编译下载好程序后，打开`SSCOM`串口通讯助手，在此处选择你的串口号。如果不知道串口号，可以在未插上串口通讯时看一下已有的串口号，插上后存在的串口号（可能会多出两个，需要一个个是，一般是多出两个的第一个）



然后选好串口后，点击打开串口



点击后，变成这样，即为串口成功打开，可以进行通讯



要确保波特率、数据位和停止位与该串口通讯的设置值一样



该值可以在$STM32CubeMX$的该串口通讯的USART下的`Parameter Setting`查看（例如，我电机使用的是USART3串口进行通讯，我就选择USART3的`Parameter Setting`）



> [!CAUTION]
>
> SSCOM中的那部分值一定要与这部分相同，不然无法进行通讯
>
> 同时，如果修改，请一定要记得重新生成代码，即右上角的`GENERATE CODE`

上述配置完成后，可以在此处选择发送选择

在这里，你可以选择定时发送，只需要在输入框中输入发送的值，然后勾选定时发送，即可实现定时发送的功能，或者手动点击发送也可以。发送示例：`V+0.5+0.5E\n`，其中，`V`和`E\n`以及符号为必须有，符号可以为`+`也可以为`-`数值可以随机改，但一般不超过1.3（最大速度设置为1.3m/s）



> [!NOTE]
>
> 如果需要修改速度，则需要在$STM32CubeMX$中修改定时器的值，本项目中选择的驱动电机的定时器为`TIM2`、`TIM3`和`TIM4`需要将这里面的`Parameter Setting`中的`Counter Period`的值增大或减小即可
>
> 
>
> 同时，如果修改，请一定要记得重新生成代码，即右上角的`GENERATE CODE` 

具体测试效果类似如下图所示，由于PID算法的存在，速度从0逐步增加，直到0.5m/s为止



### 

## HX711压力传感器

### 1 准备

- 犀牛派A1
- HX711压力传感器模块
- USB转串口模块
- STM32F407ZGT6开发板
- mini下载器
- Windows系统电脑
- 杜邦新若干

### 2 硬件连接

将HX711与$STM32F407ZGT6通过杜邦线相连，USB转串口通过杜邦线与STM32F407相连，USB接电脑，下载器通过杜邦线与STM32F407直接相连，USB接电脑，按照如下接线

串口转`TTL`接线

```bash
GND -> GND
TXD -> PD9
RXD -> PD8
# 以下三个串口均为供电串口，三选一接即可
VCC -> 5V/3V3
3V3 -> 3V3
5V -> 5V
```

下载器连接`STM32F407ZGT6`（为单片机供电）

```
GND -> GND
SWC -> CLK
SWD -> DIO
3V3 -> 3V3
# 第二种供电（通讯）方式
Type-c直连USB UART
```

压力传感器模块连接`STM32F407ZGT6`

```
# 首先将压力传感器与称重的连接好（会有线连接，注意防呆）
# 然后按照对应的线与引脚连接
# 左侧红线对应右侧第一个引脚，黑线对应右侧第二个引脚
# 白线对应右侧第三个引脚，绿线对应右侧第四个引脚
GND -> GND
DT -> PE9
SCK -> PE8
VCC -> 3V3
```

ba555c076db084623fa411c953d653ff

### 3 测试

打开 `keil` 项目的 [test_us.uvprojx 文件](.\code_part\test_code\嵌入式部分\FreeRTOS\MDK-ARM\test_us.uvprojx)

点击`freertos.c` ，看到



屏蔽所有任务只保留 `StartTask08` 



`StartTask08` 任务内容如下



编译上传 STM32 之后，打开PC端串口助手，看到输出

注：质量数据没有去皮



## OLED显示屏

### 1 准备

- 犀牛派A1
- OLED显示屏
- USB转串口模块
- STM32F407ZGT6开发板
- mini下载器
- Windows系统电脑
- 杜邦新若干

### 2 硬件连接

将OLED与STM32F407ZGT6通过杜邦线相连，USB转串口通过杜邦线与STM32F407相连，USB接电脑，下载器通过杜邦线与STM32F407直接相连，USB接电脑，按照如下接线

串口转`TTL`接线

```bash
GND -> GND
TXD -> PD9
RXD -> PD8
# 以下三个串口均为供电串口，三选一接即可
VCC -> 5V/3V3
3V3 -> 3V3
5V -> 5V
```

下载器连接`STM32F407ZGT6`（为单片机供电）

```
GND -> GND
SWC -> CLK
SWD -> DIO
3V3 -> 3V3
# 第二种供电（通讯）方式
Type-c直连USB UART
```

`OLED`连接`STM32F407ZGT6`

```
GND -> GND
VCC -> VCC
SCL -> PB6
SDA -> PB7
```

0d1626446b1d06d0e2905192309af2b8

### 3 测试

打开 `keil` 项目的 [test_us.uvprojx 文件](.\code_part\test_code\嵌入式部分\FreeRTOS\MDK-ARM\test_us.uvprojx)

点击 `freertos.c` ，看到



屏蔽所有任务只保留 `start_oled_debug_task` 



`start_oled_debug_task` 任务内容如下



编译上传 STM32 之后，OLED屏上显示

6c133167b2890dfa56cd899dc346bf75

## DS18B20温度传感器

### 1 准备

- 犀牛派A1
- DS18B20温度传感器
- Windows系统电脑
- STM32F407ZGT6开发板
- mini下载器
- 杜邦新若干
- USB转串口模块

### 2 硬件连接

将DS18B20与STM32F407ZGT6通过杜邦线相连，USB转串口通过杜邦线与STM32F407相连，USB接电脑，下载器通过杜邦线与STM32F407直接相连，USB接电脑，按照如下接线

串口转`TTL`接线

```bash
GND -> GND
TXD -> PD9
RXD -> PD8
# 以下三个串口均为供电串口，三选一接即可
VCC -> 5V/3V3
3V3 -> 3V3
5V -> 5V
```

下载器连接`STM32F407ZGT6`（为单片机供电）

```
GND -> GND
SWC -> CLK
SWD -> DIO
3V3 -> 3V3
# 第二种供电（通讯）方式
Type-c直连USB UART
```

温度传感器模块（`DS18B20`）连接`STM32F407ZGT6`

```
GND -> GND
DIO -> PB15
VCC -> 3V3
```

3cd35ca8bbacf663c66e047f2ba35202

### 3 测试

打开 `keil` 项目的 [test_us.uvprojx 文件](.\code_part\test_code\嵌入式部分\FreeRTOS\MDK-ARM\test_us.uvprojx)

点击 `freertos.c` ，看到



屏蔽所有任务只保留 `start_collect_task`



`start_collect_task` 任务内容如下



编译上传 STM32 之后，打开PC端串口助手，看到输出



## DFRobot湿度传感器

### 1 准备

- 犀牛派A1
- DFRobot电容式土壤湿度传感器
- Windows系统电脑
- STM32F407ZGT6开发板
- mini下载器
- 杜邦新若干
- USB转串口模块

### 2 硬件连接

将DFRobot与STM32F407ZGT6通过杜邦线相连，USB转串口通过杜邦线与STM32F407相连，USB接电脑，下载器通过杜邦线与STM32F407直接相连，USB接电脑，按照如下接线

串口转`TTL`接线

```bash
GND -> GND
TXD -> PD9
RXD -> PD8
# 以下三个串口均为供电串口，三选一接即可
VCC -> 5V/3V3
3V3 -> 3V3
5V -> 5V
```

下载器连接`STM32F407ZGT6`（为单片机供电）

```
GND -> GND
SWC -> CLK
SWD -> DIO
3V3 -> 3V3
# 第二种供电（通讯）方式
Type-c直连USB UART
```

湿度传感器（`DFRobot`）连接`STM32F407ZGT6`

```
A -> PA1
+ -> 3V3
- -> GND
```

c10906b01c365f015dca267ee8d8519a

### 3 测试

打开 `keil` 项目的 [test_us.uvprojx 文件](.\code_part\test_code\嵌入式部分\FreeRTOS\MDK-ARM\test_us.uvprojx)

点击 `freertos.c` ，看到



屏蔽所有任务只保留 `start_collect_task`



`start_collect_task` 任务内容如下



# 嵌入式部分

## 1.软件需求

### （1）Keil uvision5 MDK

`Keil uvision5 MDK`安装包：https://pan.baidu.com/s/5tx8NAAUpELTvOPtTsQl-Vg

`Keil uvision5 MDK`安装流程：https://mp.weixin.qq.com/s/63JQncEWlw8oFK8lX9IV4A

### （2）STM32CubeMX

`STM32CubeMX`安装包：[【正点原子STM32】STM32CubeMX入门(搭建Java运行环境、STM32CubeMX安装、新建STM32CubeMX工程步骤、STM32CubeMX用户使用手册)-CSDN博客](https://blog.csdn.net/m0_62140641/article/details/135683008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)

`STM32CubeMX`安装流程：[【正点原子STM32】STM32CubeMX入门(搭建Java运行环境、STM32CubeMX安装、新建STM32CubeMX工程步骤、STM32CubeMX用户使用手册)-CSDN博客](https://blog.csdn.net/m0_62140641/article/details/135683008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)

`STM32CubeMX`使用教程：[【正点原子STM32】STM32CubeMX入门(搭建Java运行环境、STM32CubeMX安装、新建STM32CubeMX工程步骤、STM32CubeMX用户使用手册)-CSDN博客](https://blog.csdn.net/m0_62140641/article/details/135683008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)

### （3）SSCOM串口通讯助手

`SSCOM`安装包：[百度网盘 请输入提取码](https://pan.baidu.com/share/init?surl=6xUcdI4pRaaCjPcHwjgPQA&pwd=mc4x)

`SSCOM`安装流程：解压后直接双击打开使用

在这里插入图片描述

`SSCOM`使用教程：[【工具】SSCOM V5.13.1串口工具-基础使用（图文详情）-CSDN博客](https://blog.csdn.net/qq_41539778/article/details/135965840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)

### （4）PCtoLCD2022（OLED屏显）

`PCtoLCD2002`使用教程：[LCD / OLED显示汉字，取模软件PCtoLCD2002完美版-CSDN博客](https://blog.csdn.net/luyibing2017/article/details/125317599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)

### （5）STM32F407芯片包下载

`STM32F407`芯片包下载：[STM32F407固件库的下载与安装_stm32f407固件库下载-CSDN博客](https://blog.csdn.net/rain_turns_shade/article/details/147116903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芯片包下载&spm=1018.2226.3001.4187)

### （6）关于串口重定向

串口重定向是在使用串口通讯助手时，要将单片机返回值打印在屏上的工具，即`printf`，详看

https://blog.csdn.net/struggle_success/article/details/134621868



## 2.代码准备

### （1）相关程序下载（GitHub）

从此部分下载嵌入式部分相关程序

[ztChina/aidlux_work: 基于APLUX犀牛派A1开发板QC6490的AI聊天植物机器人，集成嵌入式、大语言模型、SLAM、视觉检测、机械设计](https://github.com/ztChina/aidlux_work?tab=readme-ov-file)

下载流程：首先，打开上述链接，如图所示方式下载



或者进入文件夹[嵌入式部分](.\code_part\test_code\嵌入式部分)

### （2）项目工程文件展示与介绍

下载完成后，打开其中的嵌入式部分



其中，每个部分具体完成任务请查看嵌入式部分中的`readme.md`文件。

以嵌入式文件夹中的`motor`文件夹为例，该文件夹主要完成了控制电机转动的程序

在这部分文件夹中，这一文件主要完成电机相关引脚等的配置



如若在打开过程中出现如下界面，此为版本问题冲突，请选择`continue`



电机控制的总代码则在MDK-ARM中的`motor`，双击打开如下图所示文件



打开后界面如下所示：



## 3.前期准备

本次实验所用到的开发板为`STM32ZGT6`开发板

[正点原子最小系统板STM32F4单片机+Mini下载器×1](https://detail.tmall.com/item.htm?id=609293805821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)

[轮趣科技TB6612电机驱动板](https://item.taobao.com/item.htm?id=43963555491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)

正点原子`ATK-BLE04/05`双模蓝牙串口，[ATK-BLE05插针版](https://detail.tmall.com/item.htm?id=927120447130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)

力士微型蠕动泵`LFP101ADB`，[（0.1-2ml/min）3V固定流量](https://item.taobao.com/item.htm?id=675821328866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)

温度传感器：[DS18B20防水型温度传感器](https://e.tb.cn/h.h6nIHdvm45txDnt?tk=NhDf4ZaaVHe)

湿度传感器：[DFRobot电容式土壤湿度传感器模块干湿度检测](https://e.tb.cn/h.h6ps4ZP2IEKIbNw?tk=YQNT4ZabD9y)

`USB`转`TTL`， [CH340模块小板](https://detail.tmall.com/item.htm?id=41323941056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)

压力传感器：[HX711](https://detail.tmall.com/item.htm?id=689424092425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)

[12V10A电源分接线 DC5.5一分三电源线5.5*2.1](https://item.taobao.com/item.htm?id=608066889564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)

电池，[12V9000mAh+2A充电器](https://item.taobao.com/item.htm?id=558538974777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)

杜邦线： 母对母 公对公 公对母，[40CM纯铜](https://detail.tmall.com/item.htm?id=42363282832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)

`OLED`屏：[0.96寸白色OLED模块/4针](https://item.taobao.com/item.htm?id=960905118150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)

电机（轮趣科技）：[MG513直流减速电机马达带GMR霍尔编码器](https://detail.tmall.com/item.htm?id=645920794388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)

继电器：[1路12V（红板支持高低电平触发）](https://detail.tmall.com/item.htm?id=41231430731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)

稳压板：[DC3.3V DC5V DC可调](https://e.tb.cn/h.h5z13UV3pOqWWmB?tk=4aj2VBw9tPO)

## 4.硬件需求（在这部分，左侧均为任意外设，右侧均为`STM32F407ZGT6开发板`）

### （1）电机驱动板与`STM32`接线

1.电机驱动板`Input_IO`接线，从下向上

```
PWMA -> PB10
AIN2 -> PD1
AIN1 -> PD0
STBY -> PB2
BIN1 -> PD2
BIN2 -> PD3
PWMB -> PB11
```

2.电机驱动板`Output_IO`接线，从上向下

```
E2B -> PD13
E2A -> PD12
E1B -> PA7
E1A -> PA6
GND -> STM32的GND
```

### （2）电机驱动板与电机接线

```
排线两头分别插电机和电机驱动板上即可
```

### （3）串口转`TTL`接线

```bash
GND -> GND
TXD -> PD9
RXD -> PD8
# 以下三个串口均为供电串口，三选一接即可
VCC -> 5V/3V3
3V3 -> 3V3
5V -> 5V
```

### （4）下载器连接`STM32F407ZGT6`（为单片机供电）

```
GND -> GND
SWC -> CLK
SWD -> DIO
3V3 -> 3V3
# 第二种供电（通讯）方式
Type-c直连USB UART
```

### （5）蓝牙模块连接`STM32F407ZGT6`

```
VCC -> 3V3
GND -> GND
TXD -> PA3
RXD -> PA2
```

### （6）温度传感器模块（`DS18B20`）连接`STM32F407ZGT6`

```
GND -> GND
DIO -> PB15
VCC -> 3V3
```

### （7）压力传感器模块连接`STM32F407ZGT6`

```
# 首先将压力传感器与称重的连接好（会有线连接，注意防呆）
# 然后按照对应的线与引脚连接
# 左侧红线对应右侧第一个引脚，黑线对应右侧第二个引脚
# 白线对应右侧第三个引脚，绿线对应右侧第四个引脚
GND -> GND
DT -> PE9
SCK -> PE8
VCC -> 3V3
```

### （8）湿度传感器（`DFRobot`）连接`STM32F407ZGT6`

```
A -> PA1
+ -> 3V3
- -> GND
```

### （9）`OLED`连接`STM32F407ZGT6`

```
GND -> GND
VCC -> VCC
SCL -> PB6
SDA -> PB7
```

### （10）水泵连接`STM32F407ZGT6`（这一部分需要使用到继电器与稳压板）

```
+ -> COM（继电器）
NO -> 12V（稳压板）
IN -> PC6（STM32F407ZGT6）
DC- -> GND（稳压板）
DC+ -> 12V（稳压板）
```

### （11）稳压板直接接电源

## 5.CubeMX相关配置介绍

> [!CAUTION]
>
> 每次修改完`STM32CubeMX`中的任意配置后，无论什么配置，请点击右上角的`GENERATE CODE`记住后请继续往下看
>
> 
>
> 如果你没打开Keil，那么就直接在弹出的界面中选择`Open Project`即可
>
> 
>
> 如果打开了，那么你有两个选择
>
> **选择一：**点击`GENERATE CODE`后，如上述操作，关掉之前那个项目即可
>
> **选择二：**点击`GENERATE CODE`后，在原项目中会弹出如下所示的选项框，选择是即可，就无需去管上述操作了
>
> 

打开`STM32CubeMX`后，选`ACCESS TO MCU SELECTOR`



这一界面中输入`STM32F407ZGT6`



此时，右侧界面中选择`STM32F407ZGT6`，双击打开即可



在如下界面中，左侧为相关配置，右侧为该芯片引脚配置



随意点击一个引脚，将其配置成需要的模式即可



在左侧找到需要的功能，此处以USART1（通讯串口）为例



选择这一功能后，在该界面中，调成这一模式



开启后，具体功能如图所示



在项目生成这里，这部分需要手动进行修改，`Project name`需要自己手动命名，`Toolchain/IDE`需要选择MDK-ARM（绑定Keil使用）



在`Code Generator`选项中，请保持与我一样的勾选



完成配置后，点击`GENERATE CODE`然后`open Project`



## 6.Keil相关配置讲解

### （1）必要介绍

在测试时，需要按照上述将线，以及程序等配置完成，`STM32`通电后，按照下面操作进行

首先，打开代码后，呈现这样界面



这是整个项目框架图



在这之后，打开main.c文件，进行任务程序的添加



> [!CAUTION]
>
> 任务代码需要在如下图所示的注释对中添加，不然下次打开会被删除
>
> 

### （2）`Keil`文件管理

首先新建一个文件（Ctrl+N或者看图）



然后保存该文件Ctrl+S或者看图



弹出的界面中，将这个文件重命名，如`motor_control`



然后点击文件包管理按钮



弹出这个界面

在这一界面中，左侧栏为项目工程文件夹，中间栏为该项目下的文件夹，右侧栏为该项目某一文件夹中的相关文件



在`Groups`栏中，点击该按钮为新建一个文件夹，如果是新项目，则需要新建一个`SYSTEM`文件夹，用于存放外设函数封装后的程序。



在这一界面中（通常为`SYSTEM`），选择`Add Files`，将刚才新建的文件添加到这里



新建一般一个.c文件，一个.h文件，两个都需要加

在选择完需要添加的文件后，点击右侧的`Add`按键，添加完成后关掉这个窗口，回到前一个窗口，点击`OK`按钮，即可将文件添加到工程文件中



关掉上述窗口窗口，回到主程序文件后，即可看到在项目工程目录中已经存在这个文件



然后，需要进行头文件路径配置，不然会有问题

点击这里（魔法棒）



然后选择`C/C++`



点击这里



弹出界面中选择这个



然后在新行中加入刚刚创建的文件夹的路径即可，示例如下所示：



### （3）关于配置

在测试程序之前，我们需要先进行程序编译，即按下编译程序按键，然后点击相关配置按键，即魔法棒



首先在这个界面



***目前常用的下载器有两种，（1）ST-Link（2）CMSIS***

（1）如果是**ST-Link下载器**，则选择



（2）如果是**CMSIS下载器**，则选择



然后点击`setting`按键，进入其它相关配置





按照如下配置

配置完成之后，点击`OK`



然后返回到代码界面，点击`Load`按键



耐心等待片刻，程序就被烧录到单片机上了。

> [!CAUTION]
>
> 在下载时，需要将ST-Link或CMSIS按照第4中的下载器连接`STM32F407ZGT6`（为单片机供电）接好，然后`USB`接电脑方可进行下载

> [!WARNING]
>
> 如遇到下载报错问题，请优先检查软件方面，检查编译后软件是否出现报错，版本不匹配等问题，其次检查接线是否接好
>
> 

## 7.程序测试

在这一部分需要先按照第四部分完成接线操作（需要测试哪一个模块接哪部分的线即可，但是OLED的接线每一个项目都需要接）

接好线之后打开对应部分的代码工程文件

### （1）motor

在这一部分，请确保STM32F407ZGT6通电，电机驱动板通电，接线没有短路，断路等情况，并且电机驱动板开关常开

确保通讯线接好，按照上述第四步的第三点，`USB`连接电脑，下载好程序后，打开`SSCOM`串口通讯助手，在此处选择你的串口号。如果不知道串口号，可以在未插上串口通讯时看一下已有的串口号，插上后存在的串口号（可能会多出两个，需要一个个是，一般是多出两个的第一个）



然后选好串口后，点击打开串口



点击后，变成这样，即为串口成功打开，可以进行通讯



要确保波特率、数据位和停止位与该串口通讯的设置值一样



该值可以在STM32CubeMX的该串口通讯的USART下的`Parameter Setting`查看（例如，我电机使用的是USART3串口进行通讯，我就选择USART3的`Parameter Setting`）



> [!CAUTION]
>
> SSCOM中的那部分值一定要与这部分相同，不然无法进行通讯
>
> 同时，如果修改，请一定要记得重新生成代码，即右上角的`GENERATE CODE`

上述配置完成后，可以在此处选择发送选择

在这里，你可以选择定时发送，只需要在输入框中输入发送的值，然后勾选定时发送，即可实现定时发送的功能，或者手动点击发送也可以。发送示例：`V+0.5+0.5E\n`，其中，`V`和`E\n`以及符号为必须有，符号可以为`+`也可以为`-`数值可以随机改，但一般不超过1.3（最大速度设置为1.3m/s）



> [!NOTE]
>
> 如果需要修改速度，则需要在STM32CubeMX中修改定时器的值，本项目中选择的驱动电机的定时器为`TIM2`、`TIM3`和`TIM4`需要将这里面的`Parameter Setting`中的`Counter Period`的值增大或减小即可
>
> 
>
> 同时，如果修改，请一定要记得重新生成代码，即右上角的`GENERATE CODE` 

具体测试效果如下图所示，由于PID算法的存在，速度从0逐步增加，直到0.5m/s为止



### （2）HX711





### （3）OLED

6c133167b2890dfa56cd899dc346bf75

8ab121334d2b0852e9593fc095be2388

OLED任务模块



### （4）蓝牙



蓝牙任务模块



### （5）DS18B20





### （6）DFRobot





## 该部分Q&A

Q：为什么我的 STM32 烧录后没有反应，串口助手也没数据？
A：先确认电路，GND 一定要共地；再看串口波特率是不是和代码一致。还有个大坑，TXD / RXD 很容易接反。

Q：我的 OLED 一直黑屏，感觉它在装死。
A：检查供电电压，OLED 有 3.3V 和 5V 版本，接错直接罢工。再看 SDA/SCL 有没有交叉接，最后确认   CubeMX 里 I2C 打开没。

Q：水泵不转，是不是坏了？           
A：别急，先看继电器有没有吸合（听不见“哒”的一声大概率没动作），再确认电机电源够不够力。TB6612 的 STBY 引脚要拉高，不然电机永远沉睡。

Q：Keil 提示 `xxx.h not found`，我人麻了。
A：经典问题，你没在魔法棒里加头文件路径。打开 C/C++ 选项，加上新建文件夹的路径就行。

Q：我用 CubeMX 配置 UART，结果编译没错，运行没反应。
A：CubeMX 最常见的坑就是引脚冲突，你看看是不是 UART 跟其他外设抢了脚。还有，时钟树要分配好，不然 UART 不会吐字。

# 视觉部分

## 1、运行环境

在终端执行以下命令，更新aidlite

```shell
sudo aid-pkg update

sudo aid-pkg install aidlite-sdk

# 确认当前可下载版本正确名称

aid-pkg list

# 安装 AidLite (select QNN version)

sudo aid-pkg install aidlite-qnn231
```

## 2、算法部署

### 2.1 模型下载

访问阿加犀模型广场https://aiot.aidlux.com/zh/models

模型广场包含了数百个不同功能的主流开源模型，针对不同硬件平台进行了适配优化，并提供了经过实测的基准性能指标作为参考。开发者可根据实际要求，快速完成评估，而无需投入大量成本和长时间等待。

同时，模型广场还提供了可直接运行的模型推理示例代码，极大的降低了开发者在已有硬件设备上测试模型性能及 AI 功能代码开发的难度和工作量，并缩短了整个流程时间，加速了方案的落地。我们搜索需要的yolov5算法进行下载，设置如下模型下载

将下载好的文件解压后通过ssh发送给开发板，可以使用xftp、MobaXterm等工具，也可以直接将压缩包发给开发板，使用unzip工具解压。

### 2.2 模型快速测试

模型运行支持c++和python方式，我们这里选择python

```shell
cd model_farm_yolov5n_qcs6490_qnn2.31_int8_aidlite
python3 python/run_test.py
```

可以看到python文件夹下生成检测结果图，模型就简单部署完成了！

yolov5s_result

如果出现以下报错提示

模型报错1

请检查aidlite更新，确定qnn版本与模型匹配

### 2.3 修改模型

找到draw_detect_res函数，修改如下，让其可视化中心原点。

```python
def draw_detect_res(img, det_pred):
    '''
    检测结果绘制
    '''
    img = img.astype(np.uint8)
    color_step = int(255 / len(coco_class))
    for i in range(len(det_pred)):
        x1, y1, x2, y2 = [int(t) for t in det_pred[i][:4]]
        score = det_pred[i][4]
        cls_id = int(det_pred[i][5])

        print(i + 1, [x1, y1, x2, y2], score, coco_class[cls_id])

        cv2.putText(img, f'{coco_class[cls_id]}', (x1, y1 - 6), 	cv2.FONT_HERSHEY_SIMPLEX, 0.5, (255, 255, 255), 1)
        cv2.rectangle(img, (x1, y1), (x2 + x1, y2 + y1), (0, int(cls_id * color_step), int(255 - cls_id * color_step)),
                      thickness=2)
        
        # 计算中心点坐标
        cx = x1 + x2 // 2
        cy = y1 + y2 // 2

        # 在中心点画一个半径为5的实心圆点
        cv2.circle(img, (cx, cy), radius=5, color=(0, 0, 255), thickness=-1)

    return img
```

找到main中 的代码段

```python
det_pred[np.isnan(det_pred)] = 0.0
```

在其上方插入以下代码，作用是输出人类类别中检测面积最大的那一个，并返回中心坐标。这一步的目的是让小车获取到最接近的人的坐标信息。

```python
# 取出所有person
person_det = det_pred[det_pred[:, 5] == 0]
det_pred = person_det
# 输出面积最大框的中心像素坐标（不用置信度高低判断）
if len(person_det) > 0:
	# 先将 xywh 转换为 xyxy
	boxes_xyxy = xywh2xyxy(person_det[:, :4])
	# 提取 x1, y1, x2, y2
	x1 = boxes_xyxy[:, 0]
	y1 = boxes_xyxy[:, 1]
	x2 = boxes_xyxy[:, 2]
	y2 = boxes_xyxy[:, 3]        
	areas = (x2 - x1) * (y2 - y1)
	# 找到面积最大的框的索引
	best_index = np.argmax(areas)
	# 取出面积最大的person框
	best_person = person_det[[best_index]]  # 使用 [[index]] 保持二维数组结构
	det_pred = best_person
else:
	print("未检测到 person")
```

再次运行代码效果如下

yolov5s_result2

关于多余的打印和保存，可以自行通过Ctrl+F全局查找关键字print屏蔽信息，在main函数中有如下几行代码，是对命令行参数的解析和赋值，当文件路径变更时，可以自行根据需求赋值。

```python
def main():
    args = parser_args()
    target_model = args.target_model
    model_type = args.model_type
    size = int(args.size)
    imgs = args.imgs
    invoke_nums = int(args.invoke_nums)
```

## 3、相机实时检测

本项目使用的是usb相机，免驱动。将相机与开发板相连，执行以下命令检视当前的usb相机设备

```shell
ls /dev/video*
```

改写之前的main函数，创建新的yolo_detect函数以及test函数

```python
def yolo_detect(interpreter,frame, size=640, conf_thres=0.5, iou_thres=0.45):
    """
    调用 Aidlite YOLO 模型进行单帧检测
    :param interpreter: 已初始化的 interpreter
    :param frame: 输入的 BGR 图像 (opencv 读取)
    :param size: 输入模型的尺寸
    :param conf_thres: 置信度阈值
    :param iou_thres: NMS 阈值
    :return: 绘制好检测框的图像
    """
    # === 图像预处理 ===
    img_processed = np.copy(frame)
    h, w, _ = img_processed.shape
    length = max(h, w)
    scale = length / size
    ratio = [scale, scale]

    image = np.zeros((length, length, 3), np.uint8)
    image[0:h, 0:w] = img_processed
    img_input = cv2.cvtColor(image, cv2.COLOR_BGR2RGB)
    img_input = cv2.resize(img_input, (size, size))

    mean_data = [0, 0, 0]
    std_data = [255, 255, 255]
    img_input = (img_input - mean_data) / std_data
    img_input = img_input.astype(np.float32)

    # === 推理 ===
    interpreter.set_input_tensor(0, img_input.data)
    t1 = time.time()
    interpreter.invoke()
    cost_time = (time.time() - t1) * 1000

    out1 = interpreter.get_output_tensor(0)
    out2 = interpreter.get_output_tensor(1)
    out3 = interpreter.get_output_tensor(2)
    output = [out1, out2, out3]
    output = sorted(output, key=len)

    # === YOLO Head ===
    stride = [8, 16, 32]
    yolo_head = Detect(OBJ_CLASS_NUM, anchors, stride, size)

    validCount0 = output[2].reshape(1, 80, 80, 255).transpose(0, 3, 1, 2)
    validCount1 = output[1].reshape(1, 40, 40, 255).transpose(0, 3, 1, 2)
    validCount2 = output[0].reshape(1, 20, 20, 255).transpose(0, 3, 1, 2)

    pred = yolo_head([validCount0, validCount1, validCount2])
    det_pred = detect_postprocess(pred, frame.shape, [size, size, 3], conf_thres=conf_thres, iou_thres=iou_thres)

    # === 只保留 person 类别 ===
    person_det = det_pred[det_pred[:, 5] == 0]
    if len(person_det) > 0:
        boxes_xyxy = xywh2xyxy(person_det[:, :4])
        x1, y1, x2, y2 = boxes_xyxy[:, 0], boxes_xyxy[:, 1], boxes_xyxy[:, 2], boxes_xyxy[:, 3]
        areas = (x2 - x1) * (y2 - y1)
        best_index = np.argmax(areas)
        det_pred = person_det[[best_index]]
    else:
        det_pred = np.array([])

    if len(det_pred) > 0:
        det_pred[np.isnan(det_pred)] = 0.0
        det_pred[:, :4] = det_pred[:, :4] * scale

    # === 绘制检测框 ===
    res_img = draw_detect_res(frame, det_pred)
    cv2.putText(res_img, f"Inference: {cost_time:.2f}ms", (10, 30),
                cv2.FONT_HERSHEY_SIMPLEX, 0.7, (0, 255, 0), 2)

    return res_img

def test(target_model="./python/yolov5s.aidlite", model_type="qnn", size=640, camera_path='/dev/video2',cam_width=1280, cam_height=720):
    """
    通过相机调用 YOLO 模型进行实时检测
    """
    # === 创建 config ===
    config = aidlite.Config.create_instance()
    if config is None:
        print("Create config failed !")
        return False

    config.implement_type = aidlite.ImplementType.TYPE_LOCAL
    if model_type.lower() == "qnn":
        config.framework_type = aidlite.FrameworkType.TYPE_QNN
    elif model_type.lower() in ["snpe2", "snpe"]:
        config.framework_type = aidlite.FrameworkType.TYPE_SNPE2
    config.accelerate_type = aidlite.AccelerateType.TYPE_DSP
    config.is_quantify_model = 1

    # === 创建 model ===
    model = aidlite.Model.create_instance(target_model)
    if model is None:
        print("Create model failed !")
        return False

    input_shapes = [[1, size, size, 3]]
    output_shapes = [[1, 20, 20, 255], [1, 40, 40, 255], [1, 80, 80, 255]]
    model.set_model_properties(input_shapes, aidlite.DataType.TYPE_FLOAT32,
                               output_shapes, aidlite.DataType.TYPE_FLOAT32)

    interpreter = aidlite.InterpreterBuilder.build_interpretper_from_model_and_config(model, config)
    if interpreter is None or interpreter.init() != 0 or interpreter.load_model() != 0:
        print("Interpreter init/load failed !")
        return False
    print("YOLO model load success!")

    # === 打开摄像头 ===
    cap = cv2.VideoCapture(camera_path, device='usb')
    if not cap.isOpened():
        print(" Cannot open camera!")
        return False

    cap.set(cv2.CAP_PROP_FRAME_WIDTH, cam_width)
    cap.set(cv2.CAP_PROP_FRAME_HEIGHT, cam_height)

    while True:
        ret, frame = cap.read()
        if not ret:
            print(" Failed to grab frame")
            break

        # 调用 YOLO 检测函数
        res_img = yolo_detect(interpreter,frame, size=size)

        cv2.imshow("YOLO Camera Detection", res_img)

        # 按 q 退出
        if cv2.waitKey(1) & 0xFF == ord('q'):
            break

    cap.release()
    interpreter.destory()
    cv2.destroyAllWindows()
    return True

if __name__ == "__main__":
    # main()
    test(target_model="./python/yolov5s.aidlite", model_type="qnn", size=640, camera_path='/dev/video2',cam_width=1280, cam_height=720)
```

将得到的usb相机设备地址名称正确填入test函数

通过aidlux网页端口访问桌面，执行代码

```python
python3 python/run_test.py 
```

可以在网页端口看到通过相机进行的实时yolo检测



至此视觉部分完成了基本框架的搭建

## 4、附测试代码

[点击打开文件](.\code_part\test_code\视觉部分\run_test.py)

# SLAM导航部分

## 软件需求

### 1.1 ROS安装

完成刷机以及`aidlux`的安装后，给开发板供电并等待指示灯亮起（根据刷机使用的系统版本不同指示灯可能会有绿色和蓝色两种不同的颜色），并使用一根`Type_c`数据线将开发板和电脑连接上



完成以上操作后，在电脑上打开拷屏软件工具[安装链接](https://file.aidlux.com/files?folder_id=ec5bf3bf),根据图中提示完成操作进入拷屏界面。

联想截图_20250826102440

如果操作正确的话会出现以下界面。

联想截图_20250826102602

使用鼠标点击界面并上滑界面解锁锁屏后使用下滑操作连接无线网，继续使用上滑操作进入如下界面，并点击`AidLux`进入`AidLUx`界面

联想截图_20250826102956

进入界面默认情况下桌面上是没有任何软件的，接下来点击界面最下方的软件仓库，在上方的分类中选择机器人选项，下载该选项下的`ROS2-Humble`和`Ubuntu Desktop`软件,密码为`aidlux`。（余下的两个软件中`Gazebo`用于`ROS`环境中的[仿真操作](https://forum.aidlux.com/t/topic/72429#p-74236-gazebo-7)，`MOveit2`用于机械臂的工控制）

联想截图_20250826103104

联想截图_20250826103818

完成以上操作后可以通过`ubuntu desktop`应用获得该开发板当前的`ip`地址和端口后，随后便可以使用`VNC`等方式通过远程连接进入开发板的`ubuntu`的界面。(密码为`aidlux`)

联想截图_20250826105050

联想截图_20250826105530

联想截图_20250826105628

进入`ubuntu`界面后在键盘上按下`Ctrl+Alt+t`打开一个终端，并在终端中输入`ros2`按下回车，等待几秒后若终端中出现以下内容则说明`ROS`环境已经正确安装，可以正常进行使用。

联想截图_20250826110140

以上便是开发板中的`ROS`环境安装操作，若不想在`AidLux`的应用商店中下载`Ros2`也可以在使用`VNC`进入`ubuntu`界面后打开终端输入[一键安装`ROS`命令]([小鱼的一键安装系列 | 鱼香ROS (fishros.org.cn)](https://fishros.org.cn/forum/topic/20/小鱼的一键安装系列))。

### 1.2 后续项目运行需要的一些依赖包安装

`colcon`构建工具:

`colcon`是一个命令行工具，用于改进编译，测试和使用多个软件包的工作流程。它实现过程自动化，处理需求并设置环境以便于使用软件包。`ROS2`中便是使用`colcon`作为包构建工具的，但是`ROS2`中没有默认安装`colcon`，需要自行安装，按下键盘上的`Ctrl+Alt+t`打开一个终端，安装命令如下。

```python
sudo apt install python3-colcon-common-extensions
```

`Joint_state_publisher`和`robot_state_publisher`的安装:

在`ROS`中，`joint_state_publisher` 和 `robot_state_publisher` 是经常一起用的两个功能包，它们各自负责不同层面的工作，但组合起来才能完整地把机器人模型在 `RVIZ` 或下游节点里“动起来”，安装命令如下。

```python
#更新软件包列表
sudo apt update

#安装 joint_state_publisher（用于发布关节状态）
sudo apt install ros-<distro>-joint-state-publisher

#安装 robot_state_publisher (接收关节状态和机器人 URDF 描述等内容)
sudo apt install ros-<distro>-robot-state-publisher

#注意：将 <distro> 替换为你的 ROS 版本（如 humble 或 melodic）

#安装 GUI 版本（可选，提供关节控制滑块,可在rviz中控制关节旋转）
sudo apt install ros-<distro>-joint-state-publisher-gui
```

`Navigation`的安装:

`Navigation`是一个开源的机器人导航框架，他的功能是让机器人安全地从`A`点移动到`B`点。路径规划、避障和自主脱困等动能是`Navigation`所具备的基本能力 ,以下内容为`apt`安装命令。

```python
# 更新软件包列表
sudo apt update

# 完整安装 Navigation Stack
sudo apt install ros-<distro>-navigation

# 或最小化安装核心组件
sudo apt install ros-<distro>-move-base ros-<distro>-amcl ros-<distro>-map-server

#注意：将 <distro> 替换为你的 ROS 版本（如 humble 或 melodic）。
```

地图服务安装：

地图服务主要用于小车完成建图后的地图保存工作。

```python
#安装地图服务
sudo apt install ros-$ROS_DISTRO-nav2-map-server 
```

## 硬件需求

雷达选用思岚—A1，该型号的雷达驱动包及相关配置文件已经整合到`rplidar_ros`和`slam_gmapping`文件夹下，故目前只需要绑定雷达端口名称。

```python
#打开一个终端输入以下命令，将rplidar_ros文件夹下的scrips文件复制到/etc/udev/rules中
cd ~/src/rpliar_ros/scripts
sudo cp rplidar.rules /etc/udev/rules.d/
```

使用`Type_c`线将雷达和电脑连接起来，并在以上操作的终端中输入`lsusb`查看雷达的端口号

```python
#输入以下命令用于查看雷达端口号
lsusb
```

联想截图_20250827101618

记住这个框起来的端口号,进入`/etc/udev/rules.d`目录 ，修改端口号

```python
cd /etc/udev/rules.d
sudo nano rplidar.rules
```

联想截图_20250827101948

修改后按ctrl+s保存，然后按ctrl+x退出，运行修改后的规则文件

```python
sudo udevadm trigger
sudo service udev reload
sudo service udev restart
```

重新拔插雷达串口，终端输入 `ll /dev/rplidar`

```python
`ll /dev/rplidar`
```

联想截图_20250827102125

出现以上内容则表示绑定成功，结尾不一定是0，根据插入设备的顺序而改变 若未出现以上内容，在点击其他位置，打开计算机，打开`dev`，在里面查找是否有` rplidar `文件

联想截图_20250827102315

如果出现，则表示连接成功。如果没有出现，可多次尝试拔插雷达串口。

接下来进行雷达测试，将雷达和电脑连接上后打开雷达开关，运行`"code_part\src\rplidar_ros\launch"`下的`rplidar_a1_launhc.py`文件。

```python
ros2 launch rplidar_ros rplidar_a1_launch.py

```

另开一个终端，在终端中输入以下内容用于查看雷达数据

```python
ros2 topic echo /scan
```

联想截图_20250827103110

在启动雷达点云图文件前先结束上文中启动的查看`/scan`话题的命令，在输入`ros2 topic echo /scan`的终端中输入`Ctrl+c`命令用于停止以上命令，然后启动`view_rplidar_a1_launch.py`文件

```python
# 启动view_rplidar_a1_launch.py文件用于在rviz中查看雷达点云图
ros2 run ${view_rplidar_a1_launch.py文件所在的功能包名}view_rplidar_a1_launch.py
```

注意：`view_rplidar_a1_launch.py`为测试文件，启动前需要将该文件从`test`文件夹中移动到正式代码文件夹`src`中，该命令中的最后一项可执行文件名称需要以python功能包中的`set.up`文件内对应的可执行文件名称为主。具体操作见[链接]([重学ROS2:（5）使用功能包组织ROS中的节点[Python/C++] - 陶小桃Blog (52txr.cn)](https://www.52txr.cn/2025/packnode.html))。

完成以上操作后新开一个终端用于启动`rviz`

```python
# 启动RVIZ
rviz2
```

启动后点击坐下角的`add`选项，在新弹出的界面中选择`by topic`下滑找到`LaserScan`将他添加到`rviz`中，如果操作正确`rviz`中将会出现以下画面

联想截图_20250827104359

## 测试

### `URDF`文件测试

在 `ROS（Robot Operating System）`中，`URDF `文件`（Unified Robot Description Format）`的主要作用是用来描述机器人模型。它是一种基于 `XML` 的文件格式，用于定义机器人的结构、几何、运动学和动力学属性。

在 `ROS `导航`（Navigation Stack）`中，`URDF `文件的作用主要是作为 机器人模型的基础描述，让导航系统能够正确理解机器人本体的结构和运动约束。它不是直接参与路径规划的核心算法，而是为导航提供必要的几何、运动学和传感器信息。总而言之在导航中，`URDF` 文件的作用是 提供机器人几何、坐标系和运动学信息，保证传感器数据、路径规划和避障计算都能正确进行。`urdf`文件的编写细则具体见[链接]([ROS中urdf文件与xacro文件的编写_xacro include urdf-CSDN博客](https://blog.csdn.net/sunkman/article/details/117365377))

本段测试用代码为[`URDF`文件](".code_part\src\slam_gmapping\urdf\robot.urdf.xacro")和将`UART`在`RVIZ`中进行可视化操作的[`display`文件](".code_part\test_code\SLAM导航部分\display.launch.py")。

```python
# 在src的上级目录下进行功能包的编译
colcon build
source install/setup.bash
# 启动urdf的可视化文件
ros2 launch ${display文件所在的功能包名} display.launch.py
```

注：display文件属于测试文件，故不包含于正式代码中，若有使用需求需要自行将文件从test文件夹中将文件取出放于正式代码文件夹`src`的功能包中（注意区分是c++还是python功能包，具体步骤见[链接]([重学ROS2:（5）使用功能包组织ROS中的节点[Python/C++] - 陶小桃Blog (52txr.cn)](https://www.52txr.cn/2025/packnode.html))。)${}括号内为将代码文件取出后所放的功能包文件夹名，若`urdf`文件的所在路径与`display`中描述的`urdf`文件路径不同则需要修改`display`文件的`urdf`文件路径内容。

启动后点击`RVIZ`左下角的`add`，下拉在新弹出的界面添加`TF`和`RobotModel`两个选项。

联想截图_20250826140650

完成以上操作后在左侧的`robotmodel`的选项中将`Description Source`的选项选为`Topic`,其次在下面的`Description Topic`中选择`/robot_description`完成以上操作后便可以在`RVIZ`的中间看见一块白色物体，这是正常现象。在`RVIZ`左侧边框的最上方有一个`Fixed Frame`的选项，在其中选择你在`URDf`文件中建立的任意一个`link`部件便可以正常显示`URDf`建立的机器人模型。

联想截图_20250826150322

根据以上操作如果可以在`RVIZ`中观察到`urdf`文件描述的机器人模型则说明`urdf`文件编写正确。

### 建图测试

本部分建图测试为雷达的单独建图测试，不会涉及到小车的其他部分。

由于雷达建图时需要一个从`map`到`urdf`文件中雷达杆件的完整联通的`tf`树（具体`TF`树示例见下图），但单独使用雷达时只会启动与雷达建图有关的相关文件，并不会发布小车的`tf`关系所以需要在雷达相关文件中加入`tf`关系静态发布代码。

`tf树完整示例`：

微信图片_20250818175012_6_18

```python
#启动雷达单独建图测试文件
ros2 run rplidar_ros test_gmapping.launch.py
```

注意：测试文件位于`"code_part\test_code\SLAM导航部分\gmapping_launch.py"`路径下，使用时将该文件从`test_code`文件移动到正式文件夹中，该测试文件和正式文件夹中的建图文件同名，使用此文件进行雷达单独建图测试时请将正式代码文件夹下的同名文件文件名进行修改号运行测试文件。

启动以上文件后新开一个终端，并在终端中输入`rviz2`启动`rviz`，点击`rviz`左下角的`add`选项后在弹出的界面中点击加入`TF`和`by_topic`下的`map`选项。

完成以上操作后打开雷达开关，若之前操作正确则会在`rviz`的界面中看见以下画面

微信图片_20250828102154_64_2

若没有出现以上画面可以输入以下命令查看雷达是否被正常识别

```python
#测试代码和正式代码文件中的雷达USB接口号为USB0
ls /dev/tty*
```

注意根据USB接口接入设备的顺序先后，各个设备的`USB`号将会按照先后顺序被命名为`USB0,USB1,USB2...`，若出现雷达端口没有被正常识别的问题可以尝试重新插拔雷达`USB`接口，或者终端中输入以上命令查看雷达`USB`是否被识别。

### 导航测试

该导航部分的测试主要测试定点导航，人体识别导航和语音交互导航三个部分。

首先启动`gazebo`仿真应用，加载仿真世界和机器人模型，在终端中输入以下命令（关于`gazebo`的具体内容见[链接](https://forum.aidlux.com/t/topic/72429#p-74236-gazebo-7),`gazebo`安装教程见[链接](https://forum.aidlux.com/t/topic/72429#p-74236-ros2-humblervizgazebo-4)）

```python
#启动gazebo仿真世界，并加载机器人模型
ros2 launch ${gazebo启动文件所在功能包名} gazebo.launch.py
```

注意：由于`gazebo`文件为测试文件，使用时需将`gazebo`文件和仿真使用的`URDF`文件从`test`文件夹中移动到正式代码文件夹`src`的c++功能包中，并根据当前功能包的内容修改`gazebo`文件内的`urdf`文件路径

`gazebo`正确启动后应出现以下画面

微信图片_20250826164146_57_2

在上一步的基础上在重新打开一个终端，启动`test`文件夹中的`nav.launch.py`文件，用于启动导航功能

```python
#启动导航
ros2 launch ${nav.launch.py文件所在功能包名} nav.launch.py
```

注意：与上文的`gazebo`文件一样，启动该文件时需要将`nav.launch.py`文件和`config`与`map`文件夹从`test`文件夹中移动到正式代码文件夹`src`中的python功能包，并修改地图和配置文件的路径，其中`config`文件夹内为导航（`nav`）和建图`SLam`的配置文件，`map`文件夹下为存放通过`slam`建立的地图文件。

`nav.launch.py`文件正确启动后应该出现以下画面

微信图片_20250826164146_56_2

#### 定点导航功能测试

在完成以上启动`gazebo`仿真世界和导航文件后，保持以上两个文件的运行状态，启动定点导航的测试文件，该文件将会给机器人两个目标点(4.0)和(-4.-1)

```python
#启动定点导肮文件
ros2 run ${dingdian.py文件所在python功能包名} dingdian
```

注意：与上文一致，由于该文件为测试文件，启动是需从`test`文件夹中移动到正式文件夹`src`中的python功能包，该文件由于没有引用的部分所以没有需要修改的路径,并且该命令中的最后一项可执行文件名称需要以python功能包中的`set.up`文件内对应的可执行文件名称为主

若正确启动文件后将会在`RVIZ`中观察到机器人自动规划到达目标点的路径并跟随规划的路径前进，当到达第一个目标点后将会自动前往第二个个目标点（启动过程中若出现定点导航一直无法启动的问题可以使用`Ctrl+c`停止导航和定点导航两个文件，并重新启动）。

微信图片_20250826164146_58_2

微信图片_20250826164147_59_2

#### 语音交互导航功能测试

该部分的导航文件位于`"src\duodian\duodian\yvying_jiaohu_daohang.py"`路径下，由于该导肮文件需要与语音大模型进行交互，所以通过向该导航文件所订阅的话题发送话题消息进行测试。

在启动`gazebo`和`nav.launch.py`文件的前提下启动`yvying_jioahu_daohang.py`文件

```python
#启动`yvying_jioahu_daohang.py`文件
ros2 run duodian yvying_jiaohu_daohang
```

启动后观察该终端和启动`nav.launch.py`文件的终端内容，正常启动的情况下当`yvying_jioahu_daohang.py`文件后等待几秒两个终端都将出现新的日志内容打印并且在启动`yvying_jioahu_daohang.py`文件的终端最终应该打印初始化完成的内容，若没有出现以下内容则重新启动`yvying_jioahu_daohang.py`和`nav.launch.py`文件。

完成以上操作后，启动`test`文件夹下的`shiyan.py`文件，用于向`yvying_jioahu_daohang.py`文件订阅的话题发送导航命令

```python
#启动shiyan.py文件
ros2 run ${shiyan.py文件所在的功能包名} shiyan
```

注意：与上文一致，由于该文件为测试文件，启动是需从`test`文件夹中移动到正式文件夹`src`中的python功能包，该文件由于没有引用的部分所以没有需要修改的路径,并且该命令中的最后一项可执行文件名称需要以python功能包中的`set.up`文件内对应的可执行文件名称为主，并且该文件发送的话题消息可以根据`yvying_jiaohu_daohang.py`文件的内容修改。

启动话题发送文件后可以在终端中输入命令查看是否正确发送话题内容

```python
#查看话题发送内容
ros2 topic echo /ros_topic
```

按下回车后终端中将会每隔1秒打印发送的消息内容（以下为发送多个目标点的消息内容。具体内容因文件内容而异）

微信图片_20250826164145_53_2

若操作正确那么`RVIZ`中的小车将会执行前进3米的操作

微信图片_20250826164145_54_2

#### 人体识别导航

该部分导航文件位于`src\duodian\duodian\renti_shibi_daohang.py`下，由于该导肮文件需要与视觉部分进行交互，所以通过向该导航文件所订阅的话题发送话题消息进行测试。

在启动`gazebo`和`nav.launch.py`文件的前提下启动`renti_shibi_daohang.py`文件

```python
#启动renti_shibi_daohang.py文件
ros2 run duodian renti_shibi_daohang
```

启动完成后新开一个终端，并在启动`renti_shibi_daohang`的同级目录下输入以下内容。

```python
#输入以下命令用于启动导航
ros2 service call /start_nav std_srvs/srv/SetBool "{data: true}"
```

输入后等待几秒，启动人体识别导航的终端中将会打印出导航已经准备就绪的内容，若出现以上内容则说明导航已经正确启动，但如果没有出现则重新启动导航文件并再次输入以上命令。

应为该导航文件也是订阅特定话题并进行导航操作所以需要新开一个终端并输入以下内容

```python
#输入以下内容，用于启动人体导航
ros2 topic pub /person_box geometry_msgs/PointStamped "{header: {frame_id: 'map'}, point: {x: 2.5, y: 1.2, z: 0.5}}"
```

若以上操作正确则在输入以上命令并按下回车后`RVIZ`中的小车将会自动前往目标点

微信图片_20250826164146_55_2

# 语音对话部分

## ASR部分（语音转文字）

根据提供的[模型文件(model_farm_wenet_qcs8550_onnx_fp32_aidlite.zip)](.\code_part\test_code\语音对话部分\)下载解压，

内部含有模型文件和pyhton测试文件，

执行以下命令

```
cd model_farm_wenet_qcs8550_onnx_fp32_aidlite
python3 python/wenet_onnx_infer.py 
```

运行结果



## TTS部分（文字转语音）

在[模型广场](https://aiot.aidlux.com/zh/models?modelType=15)搜索WeTTS然后下载

wetts1

或者[打开文件(model_farm_wetts_qcs8550_onnx_fp32_aidlite.zip)](.\code_part\test_code\语音对话部分\)

解压后执行

```shell
cd model_farm_wetts_qcs6490_onnx_fp32_aidlite
#根据输入文字生成语音文件
python3 python/run_test.py --text_path "窗前明月光，疑是地上霜，举头望明月，低头思故乡" --wav_path ./python/results
#根据文本生成语音文件
python3 python/run_test.py --text_path python/chinese.txt --wav_path ./python/results
```

运行结果如下



可以在python/result目录下找到对应的wav文件

### Tips

以上能快速部署、具备完整结构的模型，我们在将其封装为一个模块以供外部调用时，可以从以下步骤进行分析（以wetts为例）

1. 先将重心放到main函数，观察其逻辑结构

   ```python
    #通过命令行获取参数后设置资源变量和生成路径
    source = args.text_path
    wav_path =args.wav_path
       
    if source.endswith(".txt"):
       ...
    else:
       ...
    
   ```

   我们在调用过程中一般都是流式的，不需要读取txt文件，也不需要打印额外输出，所以我们可以得到一个精简的do_tts()函数

   ```python
   def do_tts(text):
   
       model = load_model()
       source = text
       wav_path ='./return_results'
       if not os.path.exists(wav_path):
           os.makedirs(wav_path)
       data = replace_punctuation(source).strip()
       num=0
       for i in range(10):
           t1=time.time()
           phones, audio, frontedtime, vitstime = model.synthesis(data)
           t2=time.time()
   
           cost_time = (t2-t1)*1000
           audio_len=len(audio)/16000
           rtf = cost_time/audio_len
           num+=1
           print(f"tokens :{len(data)},The length of audio ：{audio_len}, cost time： {round(cost_time,2)} ms ")
       out_name = f"{wav_path}/{len(data)}_{data[0]}.wav"
       wavfile.write(out_name, 16000, audio)
       #返回值是文件地址，当要和其他模块对接时，可以调整这个返回值为一个音频流，而非文件
       return out_name
   ```

2. 观察模型的路径引用，当我们需要把功能模块加入到自己的工作空间时，就要尤其注意current_path，即当前的终端运行目录，当目录结构被改变时，我们就需要手动地去修改这些地方，适应我们自己的结构。

   ```python
   #从run_test中我们可以定位到这个依赖包
   from cli.model import load_model
   
   #找到它继续定位load_model()中的函数
   current_path =os.getcwd()
   # current_path=os.path.dirname(current_path)
   front_dir = f'{current_path}/models/frontend'
   backend_dir = f'{current_path}/models/multilingual'
   
   ```

## LLM部分

### 1、依赖软件包安装

1、adb获取开发板IP

2、进入web端

3、打开终端，安装python依赖包

```shell
pip install noisereduce librosa  webrtcvad torchaudio sounddevice sherpa_onnx  unidecode Levenshtein
```



4、在终端创建一个文件夹，保存待会下载的软件包，并进入

```shell
mkdir packags
cd packags
```

5、安装aidlux工具

（其中包含aidlux内网工具，需要请联系工作人员）

```shell
# 下载 aidllm 安装包
	wget https://aidllm.aidlux.com/files/aidllm_2.0.0_arm64.aid.gpg

# 安装 aidllm
	sudo aid-pkg -i -d aidllm_2.0.0_arm64.aid.gpg

# 下载 aidgen-sdk 安装包
	wget http://192.168.110.22:18080/job/aplux_aidgen/9/artifact/aidgen-sdk_1.0.0.9_arm64_ub2204.aid.gpg

# 安装 aidgen-sdk🔍 查询可⽤模型
	sudo aid-pkg -i -d aidgen-sdk_1.0.0.9_arm64_ub2204.aid.gpg

# 下载 aid-open-api 安装包
	wget https://aidllm.aidlux.com/files/aid-openai-api_2.0.0_arm64.aid.gpg

# 安装 aid-openao-api
	sudo aid-pkg -i -d aid-openai-api_2.0.0_arm64.aid.gpg
```

### 2、官方LLM模型准备和测试

1、我们使用官方的一个LLM模型作为测试之外，还会用到一个自己下载的[Qwen2.5-0.5B-Instruct_1-Q8.gguf模型](./code_part/test_code/语音对话部分/)作为最终部署。

2、官方LLM模型下载

```shell
# 查看远程支持的模型
aidlux@aidlux:~$ aidllm remote-list api
    Current Soc :  6490 

    Name                           Url                            CreateTime     
    qwen1.5-0.5B-Chat-6490         aplux/qwen1.5-0.5B-Chat-6490   2025-07-24 15:17:10
    qwen2.5-0.5B-Instruct-6490     aplux/qwen2.5-0.5B-Instruct-6490 2025-07-24 15:17:43
    MiniCPM-1B-sft-6490            aplux/MiniCPM-1B-sft-6490      2025-07-24 15:17:24
    qwen2.5-1.5b-instruct-q4_k_m   aplux/qwen2.5-1.5b-instruct-q4_k_m 2025-07-24 15:42:39
    qwen2-0.5B-Instruct-6490       aplux/qwen2-0.5B-Instruct-6490 2025-07-24 15:16:51
    Meta-Llama-3.2-1B-Instruct-6490 aplux/Meta-Llama-3.2-1B-Instruct-6490 2025-07-24 15:32:09
    
# 拉去远程模型
aidllm pull api aplux/qwen2.5-1.5b-instruct-q4_k_m

# 查看本地已下载模型列表
aidlux@aidlux:~$ aidllm list api
    qwen2.5-1.5b-instruct-q4_k_m

# 加载模型
aidlux@aidlux:~$ aidllm start api -m qwen2.5-1.5b-instruct-q4_k_m
    Use model:  qwen2.5-1.5b-instruct-q4_k_m
    Api server start successfully.
```

3、官方模型 ui 测试

```shell
# 安装 UI 前端服务，安装后web界面多出一个图标
sudo aidllm install ui
sudo aidllm start ui
```



点击图标，打开图形化使用方法，测试`你好`，有输出说明模型加载正确



4、官方模型python测试

模型开启后可以使用Web UI，参考官方链接https://docs.aidlux.com/guide/software/sdk/aidgense/aidgense，也可以直接使用本地的方式在开发板上对话模型，运行以下python测试脚本

```python
import os
import requests
import json

def stream_chat_completion(messages, model="qwen2.5-1.5b-instruct-q4_k_m"):
    """
    调用本地模型接口，流式输出助手回复
    """
    url = "http://127.0.0.1:8888/v1/chat/completions"
    headers = {"Content-Type": "application/json"}
    payload = {
        "model": model,
        "messages": messages,
        "stream": True
    }

    response = requests.post(url, headers=headers, json=payload, stream=True)
    response.raise_for_status()

    reply = ""  # 收集助手回复
    for line in response.iter_lines():
        if not line:
            continue
        line_data = line.decode('utf-8')
        if line_data.startswith("data: "):
            data = line_data[len("data: "):]
            if data.strip() == "[DONE]":
                break
            try:
                chunk = json.loads(data)
            except json.JSONDecodeError:
                print("无法解析JSON：", data)
                continue

            content = chunk["choices"][0]["delta"].get("content")
            if content:
                print(content, end="", flush=True)
                reply += content
    print()  # 换行
    return reply

def trim_history(messages, max_rounds=5):
    """
    只保留 system + 最近 max_rounds 轮 user/assistant 消息
    """
    system_prompt = messages[0]  # 第一个是 system
    other_msgs = messages[1:]
    # 每轮包含 2 条消息：user + assistant
    keep_msgs = other_msgs[-(max_rounds * 2):]
    return [system_prompt] + keep_msgs

if __name__ == "__main__":
    # 初始化对话历史
    messages = [
        {"role": "system", "content": "You are a helpful assistant."}
    ]

    while True:
        user_input = input("User: ")
        if user_input.lower() in ["exit", "quit", "q"]:
            print("结束对话。")
            break

        messages.append({"role": "user", "content": user_input})
        print("Assistant:", end=" ")
        reply = stream_chat_completion(messages)
        messages.append({"role": "assistant", "content": reply})

        # 对话裁剪
        messages = trim_history(messages, max_rounds=5)

```

运行python脚本，可以和模型对话啦！

```shell
python3 test_llm.py
```

llm对话

### 3、自己部署LLM模型

1、自己下载的[Qwen2.5-0.5B-Instruct_1-Q8.gguf模型](./code_part/test_code/语音对话部分/)

2、vscode的SSH连接开发板，进入 `/opt/aidlux/app/` 文件夹

3、在指定文件夹/opt/aidlux/app/aid-openai-api/res/models 下创建文件夹

```shell
aidlux@aidlux:/opt/aidlux/app$ cd aid-openai-api/res/models/
aidlux@aidlux:/opt/aidlux/app/aid-openai-api/res/models$ mkdir Qwen2.5-0.5B-Instruct_1-Q8
```

4、将 Qwen2.5-0.5B-Instruct_1-Q8.gguf 模型复制到该文件夹下

5、创建两个json文件

```shell
aidlux@aidlux:/opt/aidlux/app/aid-openai-api/res/models$ cd Qwen2.5-0.5B-Instruct_1-Q8/
aidlux@aidlux:/opt/aidlux/app/aid-openai-api/res/models$ vim configuration.json
内容如下:
{"framework":"Pytorch","task":"text-generation"}
```

```shell
aidlux@aidlux:/opt/aidlux/app/aid-openai-api/res/models$ vim Qwen2.5-0.5B-Instruct_1-Q8.json 
内容如下:
{
  "backend_type" : "llamacpp",
  "model":{
    "path" : "res/models/Qwen2.5-0.5B-Instruct_1-Q8/Qwen2.5-0.5B-Instruct_1-Q8.gguf"
  }
}
```

6、打开 api_cfg.json 文件，此时文件结构如下



7、在该 json 文件改为

```json
{
  "prompt_template_list": [
    {
      "qwen1.5": "<|im_start|>system\n{0}<|im_end|>\n<|im_start|>user\n{1}<|im_end|>\n<|im_start|>assistant\n"
    },
    {
      "qwen2": "<|im_start|>system\n{0}<|im_end|>\n<|im_start|>user\n{1}<|im_end|>\n<|im_start|>assistant\n"
    },
    {
      "deepseek": "<｜begin▁of▁sentence｜>{0}<｜User｜>{1}<｜Assistant｜>"
    }
  ],
  "model_cfg_list": [
    {
      "model_id": "qwen2.5-1.5b-instruct-q4_k_m",
      "model_create": "1756219500963",
      "model_owner": "aplux",
      "cfg_path": "./models/qwen2.5-1.5b-instruct-q4_k_m/qwen2.5-1.5b-instruct-q4_k_m.json",
      "prompt_template_type": "qwen2"
    },
    {
      "model_id": "Qwen2.5-0.5B-Instruct_1-Q8",
      "model_create": "1756219500964",
      "model_owner": "aplux",
      "cfg_path": "./models/Qwen2.5-0.5B-Instruct_1-Q8/Qwen2.5-0.5B-Instruct_1-Q8.json",
      "prompt_template_type": "qwen2"
    }
  ],
  "http_cfg": [
    {
      "ip": "0.0.0.0"
    },
    {
      "port": 8888
    }
  ],
  "work_folder": "/opt/aidlux/app/aid-openai-api",
  "dsp_skel_folder": "",
  "res_folder": "./res",
  "log_level": "INFO",
  "log_folder": "./logs/",
  "default_model_id": "Qwen2.5-0.5B-Instruct_1-Q8"
}
```

注：字段说明

```shell
字段说明：
model_id ：模型标识，唯⼀ ID，⽤于运⾏时指定模型，例如 qwen2.5-1.5b-instruct-q4_k_m 。

model_create ：模型注册时间戳，可使⽤命令 printf "%s%03d\n" "$(date +%s)" "$((10#$(date +%N)/ 1000000))" ⽣成，单位为毫秒。

model_owner ：模型所有者名称，可⾃定义，例如 "aplux" 。

cfg_path ：模型主配置⽂件路径，Linux 下使⽤相对路径（如 ./models/... ），Android 下需使⽤绝对路径（如 /sdcard/... ）。
		./models/qwen2.5-1.5b-instruct-q4_k_m/qwen2.5-1.5b-instruct-q4_k_m.json
		./models/qwen2.5-1.5B-instruct-8550-bin/qwen2.5-1.5b-instruct-htp.json
		注意一点为添加bin类型模型配置文件时，需要指定例如：qwen2.5-1.5b-instruct-htp.json，而非htp-backend.json

prompt_template_type ：对话提⽰模板类型，常⻅取值如 "qwen1.5" 、 "qwen2" 、 "deepseek" ，应与模型训练格式匹配。
```

8、测试

```shell
aidlux@aidlux:/opt/aidlux/app$ aidllm  stop api
Api server stop successfully.
aidlux@aidlux:/opt/aidlux/app$ aidllm  start api
Use model:  Qwen2.5-0.5B-Instruct_1-Q8
Api server start successfully.
```

Qwen2.5-0.5B-Instruct_1-Q8 启动成功

使用 ui 测试，有输出，说明成功



## RAG部分

### 1、安装软件工具包

和LLM部分一样的工具包，[安装过程跳转](#1、依赖软件包安装)

### 2、获取aidlux账号

🔐一、注册账号

访问 aidlux（[Profile | AidLux Single Sign-On](https://auth.aidlux.com/zh/user/profile)） 官⽹，注册并登录⼀个 **Aidlux** 账号。

📚 ⼆、创建 **RAG** 知识库

   1.🌐 登录 **aidllm-cms**

	打开浏览器访问 👉 https://aidllm.aidlux.com，使⽤你的 Aidlux 账号登录

   2.🧭 进⼊知识库管理界⾯

	登录后点击左侧“知识库”菜单，进⼊管理⻚⾯，点击“新建”。

    3.📝 填写知识库信息

	名称：仅⽀持英⽂字⺟和数字（如： MyRAG2025 ）。

	嵌⼊模型：选择当前已加载的 embedding 模型。

	切⽚⽅法：可选 General 或 Q&A ，具体说明如下：

| 🧩 切片方法 | 📄 支持格式 | 📖 说明 |
| --- | --- | --- |
| General | 文本（.txt / .pdf） | 将连续文本按“分段标识符”分割，再按 Token 数量不超过“最大长度”合并为一块。 |
| Q&A | .xlsx / .csv / .txt | 用于问答格式：Excel 两列（无表头：问题 / 答案）；CSV / TXT 使用 **Tab** 分隔，UTF-8 编码。 |

我们使用[zhishiku单行.txt](./code_part/test_code/语音对话部分/)作为素材常见知识库



选择Q & A模式，注意文件规范，"问：xxxx？/xxxx?"[一个tab]答：xxxxx”

```
问：你叫什么？/你的名字是什么？/你是谁？	答：专属陪伴植物机器人，小笨蛋。
问：你有什么功能？/你能干什么？	答：可以实时监测植物状态，自动浇水，还有陪伴聊天功能。
问：绿萝叶子发黄了，怎么办呀？	答：绿萝叶子发黄可能是浇水太多啦，先停几天浇水，放在通风的地方，让土壤干点就好啦
```

💻 三、命令⾏操作 **aidllm**

1. 🔑 登录远程 **cms**

```shell
aidlux@aidlux:~$ aidllm login
ACCOUNT: 你的账号
Password: 
login successfully
```

### 3、安装RAG服务

```
sudo aidllm install rag
```

📃 查看知识库列表

```shell
aidlux@aidlux:~$ aidllm remote-list rag
Name                           EmbeddingModel                 CreateTime     
tesla                          BAAI/bge-large-zh-v1.5         2025-07-25 15:16:53
Test3                          BAAI/bge-large-zh-v1.5         2025-07-28 14:03:59
Test4                          BAAI/bge-large-zh-v1.5         2025-07-30 15:04:53
treatment                      BAAI/bge-large-zh-v1.5         2025-08-05 10:25:37
```

### 4、拉取知识库，启动及测试

```shell
aidllm pull rag <知识库名称>
aidllm start rag
aidllm start rag -n <知识库名称>
aidllm stop rag
```

我是拉取了我的 Test4 知识库，

使用 `aidllm start rag -n Test4` 启动

```shell
aidlux@aidlux:~$ aidllm start rag -n Test4
Use rag:  Test4
Use model:  bge-large-zh-v1.5
Rag server starting...
Rag server starting...
Rag server starting...
Rag server start successfully.
```

在ui中打开，选择知识库，并且是基于知识库的回答，测试成功



## 硬件相关

### root权限使用音麦

我们使用的是一个USB接口可以实现音箱和麦克风两种功能的一体化设备

连接好USB之后，设备音麦设备上显示亮灯，上为音箱，下为麦，亮蓝为打开，灭或者红光为关闭



在终端中使用

```shell
aidlux@aidlux:~$ lsusb
Bus 007 Device 001: ID 1d6b:0003 Linux Foundation 3.0 root hub
Bus 006 Device 001: ID 1d6b:0002 Linux Foundation 2.0 root hub
Bus 005 Device 001: ID 1d6b:0003 Linux Foundation 3.0 root hub
Bus 004 Device 001: ID 1d6b:0002 Linux Foundation 2.0 root hub
Bus 003 Device 001: ID 1d6b:0003 Linux Foundation 3.0 root hub
Bus 002 Device 002: ID 1235:0002 Focusrite-Novation Speedio
Bus 002 Device 001: ID 1d6b:0002 Linux Foundation 2.0 root hub
Bus 001 Device 001: ID 1d6b:0002 Linux Foundation 2.0 root hub
```

看到 `Bus 002 Device 002: ID 1235:0002 Focusrite-Novation Speedio` ，说明连接到设备，但是此时执行

```shell
aidlux@aidlux:~$ aplay -l
aplay: device_list:274: no soundcards found...
```

所以为了设备权限和使用方便，是要那个 `sudo su` 转到 `root` 用户，再进行操作

### 硬件规则绑定

#### 1、lsusb查看设备号

```shell
	Bus 002 Device 003: ID 1235:0002 Focusrite-Novation Speedio
```

#### 2、在root下使用 aplay -l查看卡号和名称，输出

```shell
card 1: Y11 [Y11], device 0: USB Audio [USB Audio]
  Subdevices: 1/1
  Subdevice #0: subdevice #0
```

发现设备名称Y11，和Focusrite-Novation不一致，使用Y11作为识别名

#### 3、使用amixer 查看通道

```shell
root@aidlux:/home/aidlux/aidcode/test#amixer -c 1
Simple mixer control 'PCM',0
  Capabilities: pvolume pswitch pswitch-joined
  Playback channels: Front Left - Front Right
  Limits: Playback 0 - 4096
  Mono:
  Front Left: Playback 819 [20%] [3.19dB] [on]
  Front Right: Playback 819 [20%] [3.19dB] [on]
Simple mixer control 'Mic',0
  Capabilities: cvolume cswitch cswitch-joined
  Capture channels: Front Left - Front Right
  Limits: Capture 0 - 4096
  Front Left: Capture 4096 [100%] [16.00dB] [on]
  Front Right: Capture 4096 [100%] [16.00dB] [on]
```

设备唯一暴露的音量play控制项（声音输出通道）为PCM

#### 4、创建文件/usr/local/bin/set-usb-audio-volume.sh

<span style="color:red">并使用chmod +x增加执行权限，否则规则文件命令没有执行权</span>

```shell
#!/bin/bash

# 获取 Y11 声卡的卡号
card_num=$(grep -m1 'Y11' /proc/asound/cards | awk '{print $1}')

# 验证卡号存在
if [ -n "$card_num" ]; then
        echo "检测到 Y11 声卡，编号为 $card_num"
        # 设置控制项
	 	amixer -c "$card_num" sset 'PCM' 20% 2>/dev/null || \
        echo "找不到匹配的控制项，需手动设置"
else
        echo "未检测到 Y11 声卡"
fi
```

#### 5、创建 udev 规则

创建一个规则文件，比如：

```shell
vim /etc/udev/rules.d/99-usb-audio-volume.rules
```

添加如下内容（替换 `1235` 和 `0002` 为你的设备 ID）：

```shell
ACTION=="add", SUBSYSTEM=="sound", ATTRS{idVendor}=="1235", ATTRS{idProduct}=="0002", RUN+="/usr/local/bin/set-usb-audio-volume.sh"
```

> #### 说明：
>
> - `ACTION=="add"` 表示设备插入时触发
> - `SUBSYSTEM=="sound"` 针对音频设备
> - `RUN+=...` 是触发脚本

#### 6、重新加载 udev 规则

```shell
udevadm control --reload-rules
```

然后重新插入你的 USB 设备，音量应该会自动设置为你脚本中设定的值。

# 机械结构部分

## 1、软件安装

		下载一个solid works三维绘图软件；资源平台软件：大工程师（现更名为大国工匠）；相应的3D打印机和配套软件。拓竹在官网下载Bambu Studio。

## 2、模型转化流程

		在模型的绘制过程中，可以通过大工程师查找标准连接件和紧固件；对于不提供标准模型的组件，可以测量其主要特征从简绘制。对器件的安装定位需要注意走线和整体配重。绘制完成后，将模型的类型导出/另存为stp文件，用于切片打印。

		或者直接使用[模型文件](./code_part/test_code/结构部分/结构)

结构整体组成见下图：

结构组成

连接件以物料表尺寸为准。

连接件组合

实物图实物图

## 3.结构附件

使用到的连接件物料

- 单通六角螺柱M3-L5 30个
- 单通六角螺柱M3-L28 3个
- 双通六角螺柱M3-L50 2个
- 双通六角螺柱M3-L80 4个
- 双通六角螺柱M4-L16 4个
- 双通六角螺柱M4-L30 5个
- 双通六角螺柱M4-L60 4个
- 双通六角螺柱M4-L80 2个
- M3螺母 57个
- M6螺母 1个
- M2×6螺钉 4个
- M3×6螺钉  30个
- M3×8螺钉 32个
- M3×10螺钉 2个
- M4×8螺钉 30个
- M6×8螺钉 1个

# 整体demo测试

## 整体外观





## 软件包准备

[ros软件包src](./code_part/src)

src软件包描述：

- camera_start_python：相机驱动
- daohang：导航
- duodian：语音交互导航，demo中没有用到，测试[SLAM导航部分](#导航测试)时用到了
- driver_node：STM32底盘驱动
- nawater_simulation：缺水语音模拟输出
- openslam_gmapping：开源建图依赖包
- slam_gmapping：建图包
- robot_core：机器人功能软件层中心控制
- rplidar_ros：雷达驱动
- sj_sj：导航和yolo桥接层 
- voice_interaction：语音交流模块
- yolov5_check：yolo检测识别

## demo流程

### 编译

1、`mkdir shouji7` 创建一个工作空间

2、将 src 文件夹放到 shouji7 文件夹

3、打开终端，进入 `shouji7/` 文件夹下

4、`colcon build`  命令行编译，可以看到同级生成了 install、log、build 文件夹

### 先SLAM建图

	建图是单独的操作流程

	1、进入web界面，打开ubuntu Desktop开启VNC服务，进入VNC



	1、打开终端，在普通用户下执行下面命令

```shell
#打开键盘控制
ros2 run teleop_twist_keyboard teleop_twist_keyboard
#开启底盘驱动节点
ros2 run  driver_node  driver_node
#打开建图
ros2 launch rplidar_ros test_gmapping.launch.py
#打开rviz2
rviz2
```

	

6、rviz中订阅/map话题，并按下雷达开关，看到中心出现雷达扫描的局部地图



3、鼠标聚焦ros2 run teleop_twist_keyboard teleop_twist_keyboard生成的终端，通过键盘操作小车运动，同时生成地图



6、保存地图在test_gmapping.launch.py中已经打开，每30秒一次，最后地图如下

		图中白色为不存在障碍物；黑色为存在障碍物，表示墙壁；灰色为不确定状态



地图默认保存在 `rplidar_ros/map/` 文件夹下，需要将生成的地图复制到daohang/map/文件夹下，才能作为导航软件包的初始地图，并注意`pgm`和`yaml`文件的名称都要为 `map`

### 再进行AI对话

语音对话和建图导航分开测试，因为：1、CPU算力不足	2、语音对话需要使用到音箱和麦克风，需要root权限，而且`sudo + 命令`无效，必须 `sudp su` 使用 root 用户；而导航和建图功能需要使用普通用户，否则报错。

1、关闭所有终端，在root下执行命令（有优先顺序）

```shell
#进入root环境
sudo su
#打开语音对话模块
ros2 launch voice_interaction voice_interaction_launch.py 
#打开核心节点，并初始启动AI
ros2 run robot_core robot_core_node 
```



2、唤醒关键词是 `"小笨蛋"`，编辑距离小于6唤醒，待唤醒后终端出现通知，并且麦克风发出声音 `我在`

注：编辑距离是你说出的文字的拼音距离 `"xiaobendan"` 的一种算法距离



3、待出现 `启动VAD录音` 后，就可以与AI交流对话



4、想结束交流，可以在 步骤3 的条件下说 `“再见”` 或者对话10秒钟没有反应，都会触发交流自动关闭信号，并且AI说出 `“再见”` 结束交流

### 输入坐标点测试导航

1、退出所有终端，在普通用户下执行（有先后顺序）

```shell
#打开导航雷达节点
ros2 launch rplidar_ros prepare_for_nav2.launch.py 
#打开底盘节点，开启odom话题
ros2 run  driver_node  driver_node
#打开导航节点和rviz
ros2 launch daohang nav2.launch.py 
#导航和yolo结合的节点
ros2 run sj_sj renti_genzhong
#打开核心节点
ros2 run robot_core robot_core_node
```



2、模拟开启导航

```shell
ros2 service call /start_nav std_srvs/srv/SetBool "{data: "True"}"
```

3、模拟发送导航点 

```shell
ros2 topic pub --once /person_box geometry_msgs/msg/PointStamped "{
  header: {frame_id: 'map'},
  point: {x: 1.0, y: 2.0, z: 0.0}
}"
```



发送点和最终话目标点一致，测试成功

### 再进行缺水寻人

1、关闭所有终端，使用普通用户，执行一下命令（有优先顺序）

```shell
#删除共享内存锁
sudo rm -f /dev/shm/fastrtps*
#打开视觉模块节点
ros2 launch yolov5_check vision.launch.py 
#开启底盘驱动节点
ros2 run  driver_node  driver_node
#打开导航雷达节点
ros2 launch rplidar_ros prepare_for_nav2.launch.py 
#打开导航节点和rviz，并加载map
ros2 launch daohang nav2.launch.py 
```



5、拨动雷达开关打开雷达



6、执行一下节点

```shell
#导航和yolo结合的节点
ros2 run sj_sj renti_genzhong 
#打开核心节点
ros2 run robot_core robot_core_node 
```

此时 `rviz` 的界面显示

注：这里的map.pgm是拿一张空白地图代替

注：图中的青蓝色阴影是雷达扫描到的障碍物



8、我们以螺丝刀作为重物，表示水盆中有水，将重物取下，模拟缺水，压力传感器数值小于预设最低值，上位机判断缺水，开启yolo和导航





9、此时，只要人员出现在小车面前，yolo就可以识别到人的方位



10、通过导航算法将小车开到人物附近，并输出语音“小笨蛋缺水了，你能帮我浇水吗”

注：第三个数据 `1.00` 是表示人物占框比例大于阈值，说明到达人物旁边

注：终端输出 `说话` 是输出语音“小笨蛋缺水了，你能帮我浇水吗”的标志输出



11、人物再将重物放回，模拟满水，小车收到满水信号，demo结束

# FAQ

## 1、web端应用无法打开

如下面显示，打不开应用

需要在板子终端执行 `sudo nginx` 重启服务，再进入web重试



## 2、web桌面不显示图标

比如ubuntu Desktop，在应用商店安装好之后，桌面应该会增加图标但是失败

需要更新 aid-desktop，重启打开 web端 就好了



## 3、使用麦克风和音箱需要使用root用户

音麦的使用需要 `sudo su` 进入 `root` 再执行和音麦相关的命令和程序

## 4、包版本冲突问题

比如一下报错，经典numpy版本冲突

```shell
aidlux@aidlux:~/aidcode/example/model_farm_yolov5n_qcs6490_qnn2.31_int8_aidlite$ python3 python/run_test.py 

A module that was compiled using NumPy 1.x cannot be run in
NumPy 2.2.6 as it may crash. To support both 1.x and 2.x
versions of NumPy, modules must be compiled with NumPy 2.0.
Some module may need to rebuild instead e.g. with 'pybind11>=2.12'.

If you are a user of the module, the easiest solution will be to
downgrade to 'numpy<2' or try to upgrade the affected module.
We expect that some modules will need time to support NumPy 2.
```

解决这种问题统一的做法是升级或者降级版本：

```shell
# 更新限制版本
pip3 install --upgrade "numpy<2"
# 版本升级
pip3 install --upgrade --force-reinstall numpy
```

## 5、无法ADB的情况下如何获取IP

1、开发板连接手机热点或者路由器

可以在手机的网络设置或者路由器的管理Web端查看

有些手机网络设置看不到，只能看到MAC，可以使用方法2

2、在板子上开启一个网络广播服务

保证PC端和开发板端在同一局域网下

PC端代码

```python
# pc_listener.py
import socket

BROADCAST_PORT = 5005
ACK_PORT = 5006

sock = socket.socket(socket.AF_INET, socket.SOCK_DGRAM)
sock.setsockopt(socket.SOL_SOCKET, socket.SO_BROADCAST, 1)
sock.bind(("", BROADCAST_PORT))

print("等待设备广播...")
while True:
    data, addr = sock.recvfrom(1024)
    msg = data.decode()
    print("收到:", msg, "来自:", addr)

    # 解析 IP 并发 ACK
    device_ip = addr[0]
    ack_sock = socket.socket(socket.AF_INET, socket.SOCK_DGRAM)
    ack_sock.sendto(b"ACK", (device_ip, ACK_PORT))
    print(f"已发送 ACK 给 {device_ip}:{ACK_PORT}")
    break
```

开发板端代码，执行过程中ip可变

```python
# device_service.py
import socket
import time
import threading

BROADCAST_PORT = 5005
ACK_PORT = 5006
MESSAGE = "Hello, I am device, my IP={}"

running = True

def get_ip():
    s = socket.socket(socket.AF_INET, socket.SOCK_DGRAM)
    try:
        # 这里不会真的发包，只是用来探测当前网卡 IP
        s.connect(("8.8.8.8", 80))
        ip = s.getsockname()[0]
    except Exception:
        ip = "0.0.0.0"
    finally:
        s.close()
    return ip

def broadcast_ip():
    global running
    sock = socket.socket(socket.AF_INET, socket.SOCK_DGRAM)
    sock.setsockopt(socket.SOL_SOCKET, socket.SO_BROADCAST, 1)

    last_ip = None
    while running:
        ip = get_ip()
        if ip != last_ip:
            print("当前 IP:", ip)
            last_ip = ip

        msg = MESSAGE.format(ip)
        sock.sendto(msg.encode(), ('255.255.255.255', BROADCAST_PORT))
        time.sleep(2)

def wait_for_ack():
    global running
    sock = socket.socket(socket.AF_INET, socket.SOCK_DGRAM)
    sock.bind(("", ACK_PORT))
    print(f"等待 PC 确认 (ACK)，端口 {ACK_PORT}...")
    while running:
        data, addr = sock.recvfrom(1024)
        if data.decode().strip() == "ACK":
            print("收到 PC 确认，退出服务。")
            running = False
            break

def main():
    t1 = threading.Thread(target=broadcast_ip, daemon=True)
    t2 = threading.Thread(target=wait_for_ack, daemon=True)
    t1.start()
    t2.start()
    while running:
        time.sleep(1)

if __name__ == "__main__":
    main()
```

开发板启动开机自启服务

```shell
aidlux@aidlux:~$ sudo mkdir -p /opt/udp_get_ip
[sudo] password for aidlux: 
aidlux@aidlux:~$ sudo cp map_bak/udp_get_ip.py /opt/udp_get_ip/
aidlux@aidlux:~$ sudo chmod +x /opt/udp_get_ip/udp_get_ip.py 
```

创建服务文件

```shell
aidlux@aidlux:~$ sudo vim /etc/systemd/system/udp_get_ip.serive
[Unit]
Description=Device IP Broadcast Service
After=network.target

[Service]
ExecStart=/usr/bin/python3 /opt/udp_get_ip/udp_get_ip.py 
Restart=on-failure
User=root
WorkingDirectory=/opt/udp_get_ip

[Install]
WantedBy=multi-user.target
```

启动

```shell
sudo systemctl daemon-reload
sudo systemctl enable udp_get_ip
sudo systemctl start udp_get_ip
```

停止

```shell
sudo systemctl stop udp_get_ip
```

查看运行状态和日志

```shell
sudo journalctl -u udp_get_ip.service -f
```

## 6、root用户使用rqt

在普通用户条件下，执行

```shell
sudo -E bash -c "source /opt/ros/humble/setup.bash && rqt_graph"
```

🧩 命令结构总览

| 部分 | 含义 |
| --- | --- |
| `sudo` | 以 **root 权限** 执行命令 |
| `-E` | **保留当前用户的静态环境变量**（如 `$DISPLAY`, `$XAUTHORITY`） |
| `bash` | 调用一个新的 **Bash shell** |
| `-c` | 后面跟的是一条 **字符串形式的命令**，供 bash 执行 |
| `"source ... && rqt_graph"` | Bash shell 要执行的具体命令串 |

🧠 深入本质：`setup.bash` 的作用不仅是设变量，还可能动态地根据环境做设置

ROS 的 `setup.bash` 做的事情远远不止于设置几个变量，它会：

1. **动态拼接环境变量**（如 `PATH`, `PYTHONPATH`, `LD_LIBRARY_PATH`）；
2. 设置 `AMENT_PREFIX_PATH`, `COLCON_PREFIX_PATH`, `CMAKE_PREFIX_PATH` 等；
3. 解析多个工作空间（如 overlay workspace）；
4. 注册插件路径；
5. 设置 Python 的包查找路径（比如 `.egg-link`, `.pth` 文件）；
6. 使用了 `eval` 和 `export` 等 Bash 行为，只在执行时生效。

## 7、lidar和串口重命名

上位机和下位机通信使用的是串口转USB，

但lidar的USB也是使用串口转USB，

所以两个设备的名称都是/dev/ttyUSB*，而且 `*` 会变，

所以使用 UDEV 设备规则固定设备的名称

1、查看设备信息

```shell
udevadm info -a -p $(udevadm info -q path -n /dev/ttyUSB0)
```

2、创建lidar设备规则

```shell
root@aidlux:/home/aidlux# vim /etc/udev/rules.d/99-usb-lidar-name.rules
```

内容：

```shell
KERNEL=="ttyUSB*",ATTRS{idVendor}=="1a86",ATTRS{idProduct}=="7523",ATTRS{bcdDevice}=="8134", SYMLINK+="my_lidar", MODE="0666"
```

3、创建串口设备规则

```shell
vim /etc/udev/rules.d/99-usb-usart-name.rules
```

内容：

```shell
ATTRS{bcdDevice}=="0264",SUBSYSTEM=="tty", ATTRS{idVendor}=="1a86",ATTRS{idProduct}=="7523",SYMLINK+="motor", MODE="0666"
```

4、重置规则

```shell
udevadm control --reload-rules
```
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

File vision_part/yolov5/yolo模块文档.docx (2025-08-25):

1、 得到模型文件

方法一：可以通过访问阿加犀模型广场：https://aiot.aidlux.com/zh/models

寻找需要的算法并进行下载即可，注意平台为Qualcomm QCS6490 ，这里举例使用yolov5模型格式转换


下载后通过可以通过ssh发送给开发板，可以使用xftp、MobaXterm等工具。

模型运行支持c++和python，这里我们使用python：首先更新aidlite，然后在解压后的一级目录中运行run_test.py文件

sudo aid-pkg update

sudo aid-pkg install aidlite-sdk

# 确认当前可下载版本

aid-pkg list

# 安装 AidLite (latest QNN version)

sudo aid-pkg install aidlite-qnn231

# 运行yolo python示例

python3 python/run_test.py

可以看到python文件夹下生成检测结果图


方法二：将自定义模型或者从模型官网下载的pt模型文件转化。

下载的pt格式一般是在英伟达环境加载，需要将其转为高通DSP硬件专属bin模型文件

(1) 更新pip版本为25.1.1

python3.10 -m pip install --upgrade pip

pip -V

(2) 安装ultralytics和onnx

pip install ultralytics onnx

(3) 设置yolo命令的环境变量

echo 'export PATH="$PATH:$HOME/.local/bin"' >> ~/.bashrc

source ~/.bashrc # 使修改立即生效

验证：执行 yolo --version，若输出版本号（如 8.3.152），则说明命令已生效。

(4) 将pt转换为onnx

新建python脚本，内容如下，并执行，可以在本文件夹生成onnx文件

#!/usr/bin/env python

from ultralytics import YOLO

# 加载同级目录下的.pt模型文件

model = YOLO('./yolov5s.pt') # 替换为实际模型文件名

# 导出ONNX配置参数

export_params = {

'format': 'onnx',

'opset': 12, # 推荐算子集版本

'simplify': True, # 启用模型简化

'dynamic': False, # 固定输入尺寸

'imgsz': 640, # 标准输入尺寸

'half': False # 保持FP32精度

}

# 执行转换并保存到同级目录

model.export(**export_params)

(5) 进入AI Model Optimizer (https://aimo.aidlux.com/)，进行ONNX格式转换为QNN支持的格式

Step1：选择模型优化，模型格式选择onnx格式上传模型


Step2：选择芯片型号以及目标框架，这里我们选择QCS6490+Qnn2.31


Step3：点击查看模型，使用Netron查看模型结构，进行输入输出的填写，使用Netron工具查看onnx模型结构，选择剪枝位置

/model.24/m.0/Conv_output_0

/model.24/m.1/Conv_output_0

/model.24/m.2/Conv_output_0


参考上图中红色框部分填写，其他不变，注意开启自动量化功能，AIMO更多操作查看使用说明或参考AIMO平台 (https://docs.aidlux.com/guide/software/ai-platform-portal-aimo)

Step4：接下来进行提交即可，转换完成后将目标模型文件下载，解压缩后其中的.bin.aidem文件即为模型文件


QNN测试代码

该代码实现了基于aidlite库的 YOLOv5 目标检测流程，主要功能包括：

命令行参数解析（模型路径、图像路径、推理次数等）；

图像预处理（等比例缩放、填充、归一化）；

使用aidlite加载模型并执行推理（支持 QNN/SNPE 框架，DSP 加速）；

推理性能统计（耗时均值、最大值、最小值、方差）；

检测结果后处理（置信度筛选、非极大值抑制 NMS、坐标映射）；

可视化检测结果（绘制边界框和类别标签，并保存图像）。

#!/usr/bin/env python3

# import sys

import os #os模块提供了与操作系统进行交互的功能。

import sys #sys模块提供了与Python解释器进行交互的函数。

import time

import aidlite

import cv2

import numpy as np

OBJ_CLASS_NUM = 80 #COCO数据集的类别数

NMS_THRESH = 0.45 #非极大值抑制的阈值

BOX_THRESH = 0.5 #检测框的置信度阈值

MODEL_SIZE = 640 #模型输入尺寸

OBJ_NUMB_MAX_SIZE = 64 #最大目标检测数

PROP_BOX_SIZE = 5 + OBJ_CLASS_NUM #每个预测框的输出维度：5 表示 (x, y, w, h, confidence)，加上 80 个类别的概率

STRIDE8_SIZE = MODEL_SIZE / 8 #特征图下采样步长为 8 的特征图大小（即 640/8=80）

STRIDE16_SIZE = MODEL_SIZE / 16

STRIDE32_SIZE = MODEL_SIZE / 32

#定义了三组不同尺度的锚框（anchor boxes），每组包含 3 个锚框。这些锚框用于生成候选框。

anchors = [

[10, 13, 16, 30, 33, 23],

[30, 61, 62, 45, 59, 119],

[116, 90, 156, 198, 373, 326],

]

#COCO 数据集中所有目标类别的名称列表，共 80 个类别。

coco_class = [

"person",

"bicycle",

"car",

"motorcycle",

"airplane",

"bus",

"train",

"truck",

"boat",

"traffic light",

"fire hydrant",

"stop sign",

"parking meter",

"bench",

"bird",

"cat",

"dog",

"horse",

"sheep",

"cow",

"elephant",

"bear",

"zebra",

"giraffe",

"backpack",

"umbrella",

"handbag",

"tie",

"suitcase",

"frisbee",

"skis",

"snowboard",

"sports ball",

"kite",

"baseball bat",

"baseball glove",

"skateboard",

"surfboard",

"tennis racket",

"bottle",

"wine glass",

"cup",

"fork",

"knife",

"spoon",

"bowl",

"banana",

"apple",

"sandwich",

"orange",

"broccoli",

"carrot",

"hot dog",

"pizza",

"donut",

"cake",

"chair",

"couch",

"potted plant",

"bed",

"dining table",

"toilet",

"tv",

"laptop",

"mouse",

"remote",

"keyboard",

"cell phone",

"microwave",

"oven",

"toaster",

"sink",

"refrigerator",

"book",

"clock",

"vase",

"scissors",

"teddy bear",

"hair drier",

"toothbrush",

]

#将边界框从中心坐标 (cx, cy, w, h) 转换为左上角和右下角坐标 (x1, y1, x2, y2)

def eqprocess(image, size1, size2):

h, w, _ = image.shape

mask = np.zeros((size1, size2, 3), dtype=np.float32)

scale1 = h / size1

scale2 = w / size2

if scale1 > scale2:

scale = scale1

else:

scale = scale2

img = cv2.resize(image, (int(w / scale), int(h / scale)))

mask[: int(h / scale), : int(w / scale), :] = img

return mask, scale

#同上，描述该函数的作用是将边界框格式转换。

def xywh2xyxy(x):

"""

Box (center x, center y, width, height) to (x1, y1, x2, y2)

"""

y = np.copy(x)

y[:, 0] = x[:, 0] - x[:, 2] / 2 # top left x

y[:, 1] = x[:, 1] - x[:, 3] / 2 # top left y

y[:, 2] = x[:, 0] + x[:, 2] / 2 # bottom right x

y[:, 3] = x[:, 1] + x[:, 3] / 2 # bottom right y

return y

#描述该函数将边界框从 (x1, y1, x2, y2) 格式转换为 (x1, y1, w, h) 格式

def xyxy2xywh(box):

"""

Box (left_top x, left_top y, right_bottom x, right_bottom y) to (left_top x, left_top y, width, height)

"""

box[:, 2:] = box[:, 2:] - box[:, :2]

return box

#描述这是一个针对单类的 NMS（非极大值抑制） 算法，用于去除冗余的边界框。

def NMS(dets, scores, thresh):

"""

单类NMS算法

dets.shape = (N, 5), (left_top x, left_top y, right_bottom x, right_bottom y, Scores)

"""

x1 = dets[:, 0]

y1 = dets[:, 1]

x2 = dets[:, 2]

y2 = dets[:, 3]

areas = (y2 - y1 + 1) * (x2 - x1 + 1)#计算面积

keep = []

index = scores.argsort()[::-1] # 按置信度从高到低排序

while index.size > 0:

i = index[0] # every time the first is the biggst, and add it directly

keep.append(i)

x11 = np.maximum(x1[i], x1[index[1:]]) # calculate the points of overlap

y11 = np.maximum(y1[i], y1[index[1:]])

x22 = np.minimum(x2[i], x2[index[1:]])

y22 = np.minimum(y2[i], y2[index[1:]])

w = np.maximum(0, x22 - x11 + 1) # the weights of overlap

h = np.maximum(0, y22 - y11 + 1) # the height of overlap

overlaps = w * h

ious = overlaps / (areas[i] + areas[index[1:]] - overlaps)

idx = np.where(ious <= thresh)[0]

index = index[idx + 1] # because index start from 1

return keep

#描述该函数将边界框裁剪到图像范围内，防止越界。

def clip_coords(boxes, img_shape):

# Clip bounding xyxy bounding boxes to image shape (height, width)

boxes[:, 0].clip(0, img_shape[1], out=boxes[:, 0]) # x1

boxes[:, 1].clip(0, img_shape[0], out=boxes[:, 1]) # y1

boxes[:, 2].clip(0, img_shape[1], out=boxes[:, 2]) # x2

boxes[:, 3].clip(0, img_shape[0], out=boxes[:, 3]) # y2

#描述该函数对模型输出进行后处理，包括筛选高置信度框、NMS 去重等操作。

def detect_postprocess(

prediction, img0shape, img1shape, conf_thres=0.25, iou_thres=0.45

):

"""

检测输出后处理

prediction: aidlite模型预测输出

img0shape: 原始图片shape

img1shape: 输入图片shape

conf_thres: 置信度阈值

iou_thres: IOU阈值

return: list[np.ndarray(N, 5)], 对应类别的坐标框信息, xywh、conf

"""

h, w, _ = img1shape

valid_condidates = prediction[prediction[..., 4] > conf_thres]

valid_condidates[:, 5:] *= valid_condidates[:, 4:5]

valid_condidates[:, :4] = xywh2xyxy(valid_condidates[:, :4])

max_det = 300

max_wh = 7680

max_nms = 30000

valid_condidates[:, 4] = valid_condidates[:, 5:].max(1)

valid_condidates[:, 5] = valid_condidates[:, 5:].argmax(1)

sort_id = np.argsort(valid_condidates[:, 4])[::-1]

valid_condidates = valid_condidates[sort_id[:max_nms]]

boxes, scores = (

valid_condidates[:, :4] + valid_condidates[:, 5:6] * max_wh,

valid_condidates[:, 4],

)

index = NMS(boxes, scores, iou_thres)[:max_det]

out_boxes = valid_condidates[index]

clip_coords(out_boxes[:, :4], img0shape)

out_boxes[:, :4] = xyxy2xywh(out_boxes[:, :4])

print("检测到{}个区域".format(len(out_boxes)))

return out_boxes

#描述该函数用于在图像上绘制检测结果，包括边界框和类别标签。

def draw_detect_res(img, det_pred):

"""

检测结果绘制

"""

img = img.astype(np.uint8)

color_step = int(255 / len(coco_class))

for i in range(len(det_pred)):

x1, y1, x2, y2 = [int(t) for t in det_pred[i][:4]]

score = det_pred[i][4]

cls_id = int(det_pred[i][5])

print(i + 1, [x1, y1, x2 + x1, y2 + y1], score, coco_class[cls_id])

cv2.putText(

img,

f"{coco_class[cls_id]}",

(x1, y1 - 6),

cv2.FONT_HERSHEY_SIMPLEX,

0.5,

(255, 255, 255),

1,

)

cv2.rectangle(

img,

(x1, y1),

(x2 + x1, y2 + y1),

(0, int(cls_id * color_step), int(255 - cls_id * color_step)),

thickness=10,

)

return img

#描述该类是 YOLOv5 的检测头，用于处理模型输出并生成最终的检测结果。

class Detect:

# YOLOv5 Detect head for detection models

def __init__(self, nc=80, anchors=(), stride=[], image_size=640): # detection layer

super().__init__()

self.nc = nc # number of classes

self.no = nc + 5 # number of outputs per anchor

self.stride = stride

self.nl = len(anchors) # number of detection layers

self.na = len(anchors[0]) // 2 # number of anchors

self.grid, self.anchor_grid = [0] * self.nl, [0] * self.nl

self.anchors = np.array(anchors, dtype=np.float32).reshape(self.nl, -1, 2)

base_scale = image_size // 8

for i in range(self.nl):

self.grid[i], self.anchor_grid[i] = self._make_grid(

base_scale // (2**i), base_scale // (2**i), i

)

def _make_grid(self, nx=20, ny=20, i=0):

y, x = np.arange(ny, dtype=np.float32), np.arange(nx, dtype=np.float32)

yv, xv = np.meshgrid(y, x)

yv, xv = yv.T, xv.T

# add grid offset, i.e. y = 2.0 * x - 0.5

grid = np.stack((xv, yv), 2)

grid = grid[np.newaxis, np.newaxis, ...]

grid = np.repeat(grid, self.na, axis=1) - 0.5

anchor_grid = self.anchors[i].reshape((1, self.na, 1, 1, 2))

anchor_grid = np.repeat(anchor_grid, repeats=ny, axis=2)

anchor_grid = np.repeat(anchor_grid, repeats=nx, axis=3)

return grid, anchor_grid

def sigmoid(self, arr):

return 1 / (1 + np.exp(-arr))

def __call__(self, x):

z = [] # inference output

for i in range(self.nl):

bs, _, ny, nx = x[i].shape

x[i] = x[i].reshape(bs, self.na, self.no, ny, nx).transpose(0, 1, 3, 4, 2)

y = self.sigmoid(x[i])

y[..., 0:2] = (y[..., 0:2] * 2.0 + self.grid[i]) * self.stride[i] # xy

y[..., 2:4] = (y[..., 2:4] * 2) ** 2 * self.anchor_grid[i] # wh

z.append(y.reshape(bs, self.na * nx * ny, self.no))

return np.concatenate(z, 1)

def show_help_prompt():

print("python3 ./qnn_yolov5_multi.py 3 Run on the DSP")

return False

def main():

argvs = len(sys.argv)

if argvs < 2:

return show_help_prompt()

acc_type = int(sys.argv[1])

aidlite.set_log_level(aidlite.LogLevel.INFO)

aidlite.log_to_stderr()

print(f"Aidlite library version : {aidlite.get_library_version()}")

print(f"Aidlite python library version : {aidlite.get_py_library_version()}")

config = aidlite.Config.create_instance()

if config is None:

print("Create config failed !")

return False

model_name = "cutoff_yolov5s_sigmoid_w8a8.qnn229.ctx.bin"

#model_name = "cutoff_yolov8x_qcs6490_w8a8.qnn231.ctx.bin" #//!模型选择

if acc_type == 1:

config.accelerate_type = aidlite.AccelerateType.TYPE_CPU

elif acc_type == 2:

config.accelerate_type = aidlite.AccelerateType.TYPE_GPU

config.is_quantify_model = 0

elif acc_type == 3:

config.accelerate_type = aidlite.AccelerateType.TYPE_DSP #//!选择DSP方式

config.is_quantify_model = 1

else:

return show_help_prompt()

config.implement_type = aidlite.ImplementType.TYPE_LOCAL

config.framework_type = aidlite.FrameworkType.TYPE_QNN229 #//!选择QNN229方式

# model_path = os.path.join(

# resource_dir, "cutoff_yolov5s_640_sigmoid_int8.serialized.bin"

# )

resource_dir = '/home/aidlux/yolov5/data/qnn_yolov5_multi/'

model_path = os.path.join(resource_dir, model_name) #加载模型

model = aidlite.Model.create_instance(model_path)

if model is None:

print("Create model failed !")

return False

#输入张量，[每次推理图像张数,图像高，图像宽，图像通道数]

input_shapes = [[1, MODEL_SIZE, MODEL_SIZE, 3]]

#三个输出层（feature map），分别对应不同尺度的目标检测[每次推理图像张数,特征图高，特征图宽，输出纬度]

#每个锚框预测 (4 + 1 + 80) = 85 个值（xywh + confidence + class probs），每层有 3 个 anchor box → 3 × 85 = 255

#三种输出，分别是检测小目标（深层特征）、中目标（中等深度特征）、大目标（浅层特征）

output_shapes = [[1, 20, 20, 255], [1, 40, 40, 255], [1, 80, 80, 255]]

model.set_model_properties(

input_shapes,

aidlite.DataType.TYPE_FLOAT32,

output_shapes,

aidlite.DataType.TYPE_FLOAT32,

)

interpreter = aidlite.InterpreterBuilder.build_interpretper_from_model_and_config(

model, config

)

if interpreter is None:

print("build_interpretper_from_model_and_config failed !")

return None

result = interpreter.init()

if result != 0:

print("interpreter init failed !")

return False

result = interpreter.load_model()

if result != 0:

print("interpreter load model failed !")

return False

print("detect model load success!")

input_tensor_info = interpreter.get_input_tensor_info()

if len(input_tensor_info) == 0 :

printf("interpreter get_input_tensor_info() failed !\n")

return False

for gi, graph_tensor_info in enumerate(input_tensor_info):

for ti, tensor_info in enumerate(graph_tensor_info):

print( f"Input tensor : Graph[{gi}]-Tensor[{ti}]-name[{tensor_info.name}]"

f"-element_count[{tensor_info.element_count}]-element_type[{tensor_info.element_type}]"

f"-dimensions[{tensor_info.dimensions}]-shape{tensor_info.shape}")

output_tensor_info = interpreter.get_output_tensor_info()

if len(output_tensor_info) == 0 :

printf("interpreter get_output_tensor_info() failed !\n")

return False

for gi, graph_tensor_info in enumerate(output_tensor_info):

for ti, tensor_info in enumerate(graph_tensor_info):

print( f"Output tensor : Graph[{gi}]-Tensor[{ti}]-name[{tensor_info.name}]"

f"-element_count[{tensor_info.element_count}]-element_type[{tensor_info.element_type}]"

f"-dimensions[{tensor_info.dimensions}]-shape{tensor_info.shape}")

stride8 = stride16 = stride32 = None

image_path = os.path.join(resource_dir, "image.jpg")

frame = cv2.imread(image_path)

frame = cv2.cvtColor(frame, cv2.COLOR_BGR2RGB)

img_input, scale = eqprocess(frame, MODEL_SIZE, MODEL_SIZE)

img_input = img_input / 255

img_input = img_input.astype(np.float32)

sum_time_0 = 0.0

sum_time_1 = 0.0

sum_time_2 = 0.0

_counter = 10

for idx in range(_counter):

st0 = time.time()

input_tensor_data = img_input.data

# result = interpreter.set_input_tensor(0, input_tensor_data)

result = interpreter.set_input_tensor("images", input_tensor_data)

if result != 0:

print("interpreter set_input_tensor() failed")

return False

et0 = time.time()

dur0 = et0 - st0

sum_time_0 += dur0

print(f"current [{idx}] set_input_tensor cost time :{dur0} ms")

st1 = time.time()

result = interpreter.invoke() #执行推理

if result != 0:

print("interpreter set_input_tensor() failed")

return False

et1 = time.time()

dur1 = et1 - st1

sum_time_1 += dur1

print(f"current [{idx}] invoke cost time :{dur1} ms")

st2 = time.time()

# stride8 = interpreter.get_output_tensor(0)

stride8 = interpreter.get_output_tensor("_326") #获取不同层级的输出张量（如 stride8、stride16、stride32）

if stride8 is None:

print("sample : interpreter->get_output_tensor() 0 failed !")

return False

print(f"len(stride8 {len(stride8)}")

# stride16 = interpreter.get_output_tensor(1)

stride16 = interpreter.get_output_tensor("_364")

if stride16 is None:

print("sample : interpreter->get_output_tensor() 1 failed !")

return False

print(f"len(stride16 {len(stride16)}")

# stride32 = interpreter.get_output_tensor(2)

stride32 = interpreter.get_output_tensor("_402")

if stride32 is None:

print("sample : interpreter->get_output_tensor() 2 failed !")

return False

print(f"len(stride32 {len(stride32)}")

et2 = time.time()

dur2 = et2 - st2

sum_time_2 += dur2

print(f"current [{idx}] get_output_tensor cost time :{dur2} ms")

print(

f"repeat [{_counter}] times , input[{sum_time_0 * 1000}]ms --- invoke[{sum_time_1 * 1000}]ms --- output[{sum_time_2 * 1000}]ms --- sum[{(sum_time_0 + sum_time_1 + sum_time_2) * 1000}]ms"

)

stride = [8, 16, 32]

yolo_head = Detect(OBJ_CLASS_NUM, anchors, stride, MODEL_SIZE)

# 后处理部分reshape需要知道模型的output_shapes

validCount0 = stride8.reshape(*output_shapes[2]).transpose(0, 3, 1, 2)

validCount1 = stride16.reshape(*output_shapes[1]).transpose(0, 3, 1, 2)

validCount2 = stride32.reshape(*output_shapes[0]).transpose(0, 3, 1, 2)

#使用 Detect 类对模型输出进行解码，得到最终的检测结果。

pred = yolo_head([validCount0, validCount1, validCount2])

#对模型输出进行后处理，得到可用的边界框和类别信息。

det_pred = detect_postprocess(

pred, frame.shape, [MODEL_SIZE, MODEL_SIZE, 3], conf_thres=0.5, iou_thres=0.45

)

#//?根据置信度最大取出best_person

# 取出所有person

person_det = det_pred[det_pred[:, 5] == 0]

det_pred = person_det

# 输出置信度最高的中心像素坐标（改为：面积最大的框）

if len(person_det) > 0:

# 先将 xywh 转换为 xyxy

boxes_xyxy = xywh2xyxy(person_det[:, :4])

# 提取 x1, y1, x2, y2

x1 = boxes_xyxy[:, 0]

y1 = boxes_xyxy[:, 1]

x2 = boxes_xyxy[:, 2]

y2 = boxes_xyxy[:, 3]

areas = (x2 - x1) * (y2 - y1)

# 找到面积最大的框的索引

best_index = np.argmax(areas)

# 取出面积最大的person框

best_person = person_det[[best_index]] # 使用 [[index]] 保持二维数组结构

det_pred = best_person

else:

print("未检测到 person")

det_pred[np.isnan(det_pred)] = 0.0

det_pred[:, :4] = det_pred[:, :4] * scale

# 提取坐标并计算中心点

x, y, w, h = det_pred[0, :4].astype(int) #x,y左上角点，w,h宽高

center_x = x + w// 2

center_y = y + h // 2

print(f"Person 中心坐标: ({center_x}, {center_y})")

print(f"x, y, w, h: {x, y, w, h}\n\n\n\n\n\n\n")

#在原始图像上绘制检测结果

res_img = draw_detect_res(frame, det_pred)

#画出中心点画一个点

cv2.circle(res_img, (center_x, center_y), radius=5, color=(0, 0, 255), thickness=20)

result = interpreter.destory()

if result != 0:

print("interpreter set_input_tensor() failed")

return False

frame_bgr = cv2.cvtColor(res_img, cv2.COLOR_RGB2BGR)

result_img_path = f"{os.path.splitext(os.path.abspath(__file__))[0]}.jpg"

cv2.imwrite(result_img_path, frame_bgr)

print(f"The result image has been saved to : {result_img_path}")

return True

if __name__ == "__main__":

main()

执行python your_code.py 3

输出图像：


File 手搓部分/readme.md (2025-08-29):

- images（保存md文件的图片）

  - xxx.png
  - xxx.jpg
  - 
- code_part（所有资料存放）

  - src(放最后开发板内软件包的版本)
    - 各种ros的软件包（软件包的名字还是不变的，可以直接引用路径）
  - test_code（各部分资料存放）
    - AI部分
      - test_llm.py
      - 
    - xxx部分
      - xxx
      - 
- 手搓文档.md（所有操作步骤）
- 手搓文档.pdf（稳定pdf版）
- readme.md
- 物料清单和传感器测试.md（单独将传感器测试拿出来作为一个文档）
- 物料明细.xlsx（所有物料清单）

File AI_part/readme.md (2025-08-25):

## 安装软件包

pip install noisereduce librosa  webrtcvad torchaudio sounddevice sherpa_onnx  unidecode Levenshtein

apt install htop

## 模型下载

除LLM之外的所有模型文件，将模型放在了百度网盘

[模型文件 (.zip)](https://pan.baidu.com/s/10DFqq1ZPpnVNQAjAnS3-EQ?pwd=fhr9)

本地部署的QWEM的LLM模型是外部下载的，放在了百度网盘

[Qwen2.5-0.5B-Instruct_1-Q8模型(.zip)](https://pan.baidu.com/s/1JcW1Q8SWhZMBVEKeUwaloQ?pwd=cs28)

本地部署的 RAG 知识库使用的的文档参考，注意知识库的格式规范

[知识库(.txt)](https://github.com/ztChina/aidlux_work/blob/main/AI_part/FAQ/%E7%9F%A5%E8%AF%86%E5%BA%93%E5%8D%95%E8%A1%8C%E6%A0%BC%E5%BC%8F.txt)

本地LLM模型和RAG模型的部署参考

[本地部署(.md)](https://github.com/ztChina/aidlux_work/blob/main/AI_part/FAQ/%E7%9F%A5%E8%AF%86%E5%BA%93%E5%8D%95%E8%A1%8C%E6%A0%BC%E5%BC%8F.txt)

## 文件夹解释
robot_core 是用来作为机器人软件层面的中心控制

voice_interaction 是所有语音模块的ros包

FAQ 是在做的过程中遇到的问题

## 可能有些细节有修改，但是整体的逻辑没变

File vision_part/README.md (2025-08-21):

### vision_part

- yolov5 :实现yolov5物体检测，包含任务检测
- rospkgs:视觉部分的使用 ros 包，一个相机驱动包，一个yolov5检测包
  - 其中yolov5_check包下qnn_yolov5_multi.py是对yolov5应用的封装和测试

#### 操作流程参考文件
[yolo模块文档 (.docx)](https://github.com/ztChina/aidlux_work/blob/main/vision_part/yolov5/yolo模块文档.docx)

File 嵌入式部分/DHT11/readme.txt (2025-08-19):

/**
 ***************************************************************************************************
 * 实验简介
 * 实验名称： DHT11数字温湿度传感器 实验
 * 实验平台： 正点原子 阿波罗 H743开发板
 * 实验目的： 学习DHT11数字温度传感器的使用

 ***************************************************************************************************
 * 硬件资源及引脚分配
 * 1 LED灯
     DS0（RED）     : LED0 - PB1
 * 2 串口1 (PA9/PA10连接在板载USB转串口芯片CH340上面)
 * 3 ALIENTEK 2.8/3.5/4.3/7寸LCD模块(包括MCU屏和RGB屏,都支持) 
 * 4 数字温湿度传感器
     DHT11 - PB12

 ***************************************************************************************************
 * 实验现象
 * 1 本实验开机的时候先检测是否有DHT11存在，如果没有，则提示错误。只有在检测到DHT11之后才开始读取
     温湿度值，并显示在LCD上，如果发现了DHT11，则程序每隔100ms左右读取一次数据，并把温湿度显示在LCD上。
 * 2 LED0闪烁, 提示程序运行。

 ***************************************************************************************************
 * 注意事项
 * 1 电脑端串口调试助手波特率必须是115200
 * 2 请使用XCOM/SSCOM串口调试助手,其他串口助手可能控制DTR/RTS导致MCU复位/程序不运行
 * 3 串口输入字符串以回车换行结束
 * 4 请用USB线连接在USB_UART,找到USB转串口后测试本例程
 * 5 P11的PA9/PA10必须通过跳线帽连接在RXD/TXD上
 * 6 4.3寸和7寸屏需要比较大电流,USB供电可能不足,请用外部电源适配器(推荐外接12V 1A电源).
 * 7 需自备DHT11数字温湿度传感器一个，并插在开发板的U4位置（根据丝印插，网面朝外）

 ***********************************************************************************************************
 * 公司名称：广州市星翼电子科技有限公司（正点原子）
 * 电话号码：020-38271790
 * 传真号码：020-36773971
 * 公司网址：www.alientek.com
 * 购买地址：zhengdianyuanzi.tmall.com
 * 技术论坛：http://www.openedv.com/forum.php
 * 最新资料：www.openedv.com/docs/index.html
 *
 * 在线视频：www.yuanzige.com
 * B 站视频：space.bilibili.com/394620890
 * 公 众 号：mp.weixin.qq.com/s/y--mG3qQT8gop0VRuER9bw
 * 抖    音：douyin.com/user/MS4wLjABAAAAi5E95JUBpqsW5kgMEaagtIITIl15hAJvMO8vQMV1tT6PEsw-V5HbkNLlLMkFf1Bd
 ***********************************************************************************************************
 */

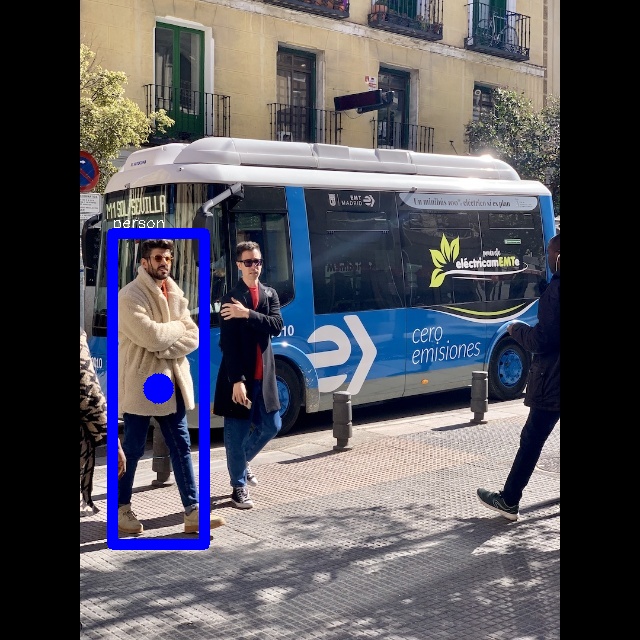
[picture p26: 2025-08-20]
vision_part/yolov5/python/qnn_yolov5_multi.jpg

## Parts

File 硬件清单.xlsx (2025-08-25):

序号 | 物料名称 | 品牌 | 型号 | 规格参数 | 图纸/购买链接
0 | 犀牛派A1 | APLUX阿加犀 | QC6490 |  | https://e.tb.cn/h.huDp7wvc6znr8JO?tk=9Nrz4PhG3og
1 | USB摄像头 | LRCP Luoke/骆日出品 |  | F1080P_3.5mm90度（无畸变） | https://item.taobao.com/item.htm?id=544215906150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
2 | 车轮（含电机 轮胎+电机 | 轮趣科技 | MG513直流减速电机马达带GMR霍尔编码器 |  | https://detail.tmall.com/item.htm?id=645920794388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
3 | TB6612电机驱动板 | 塔克创新 | TB6612 | AT8236双路直流电机带稳压驱动模块 | https://item.taobao.com/item.htm?id=785045833716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
4 | 稳压板 | 锋凌万盛 | LM2596 | DC3.3V DC5V DC可调 | https://e.tb.cn/h.h5z13UV3pOqWWmB?tk=4aj2VBw9tPO
5 | 显示屏RGB7寸 | 正点原子 |  | 【1024*600：RGB屏】 | https://detail.tmall.com/item.htm?id=609758563397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
6 | 激光雷达 | 亚博智能 | 思岚A1 | RPLIDAR A1高速版 | https://e.tb.cn/h.h5zgegAqsS95mqu?tk=rwxHVBwqzCs
7 | DHT11传感器（温湿度） | 奥松电子 | DHT11 |  | https://item.taobao.com/item.htm?id=690288699029&ns=1&priceTId=214784a317515289288315767e107d&xxc=ad_ztc
8 | 开发板STM32F4单片机+mini下载器 | 正点原子 | 最小系统板 |  | https://detail.tmall.com/item.htm?id=609293805821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

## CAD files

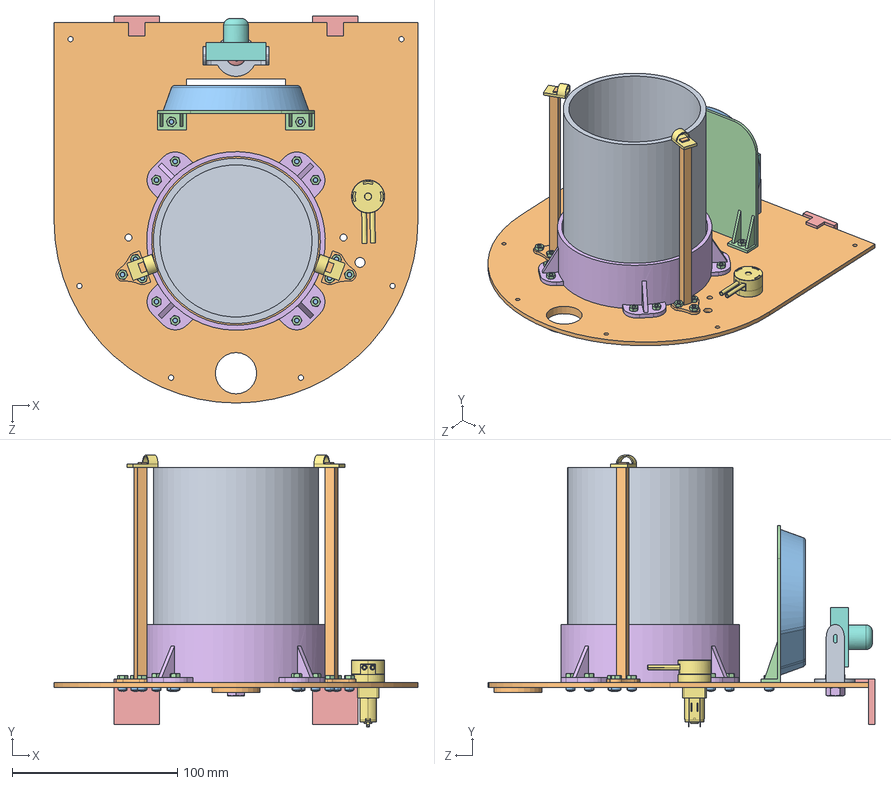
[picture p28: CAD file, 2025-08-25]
结构/上层支撑结构.SLDASM
220.0 x 164.3 x 234.0 mm
花盆100×100×130
支撑件_最顶部
一体化麦
上层竖直安装版
0.96寸led大概 x 2
花盆支撑
蠕动泵
相机
相机支架
花盆引导架 x 2
GB╱T 818-2016[十字槽盘头螺钉M3×6] x 16
六角螺母 SLMNA[SLMNA-M3] x 16
GB╱T 818-2016[十字槽盘头螺钉M6×8]
六角螺母 SLMNA[SLMNA-M6]
引导平台 x 2

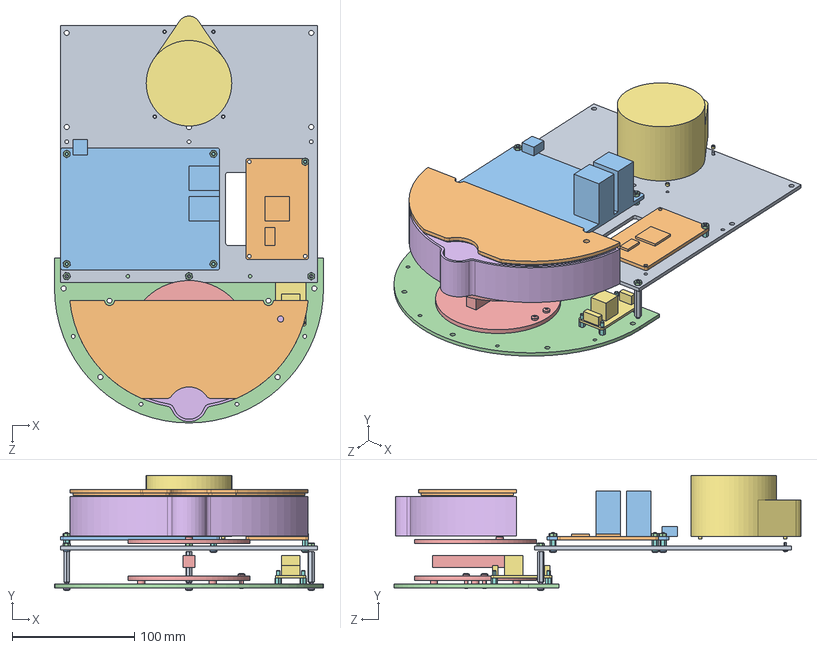
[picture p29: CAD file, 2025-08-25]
结构/中层结构装配.SLDASM
220.0 x 94.3 x 332.8 mm
支撑件_上部
stm32开发板51_2×82_8
6490开发板100×130×39.25
支撑件_最底部
压力传感器100
蓄水容器
继电器50x25x18.5
单通六角螺柱M3-L5] x 9
双通六角螺柱M3-L25] x 3
蓄水容器盖子
GB╱T 818-2016[十字槽盘头螺钉M3×4] x 4
六角螺母 SLMNA[SLMNA-M3] x 8
GB╱T 818-2016[十字槽盘头螺钉M3×10] x 2
GB╱T 818-2016[十字槽盘头螺钉M3×8] x 3
雷达
GB╱T 818-2016[十字槽盘头螺钉M3×6]
GB╱T 818-2016[十字槽盘头螺钉M2×6]

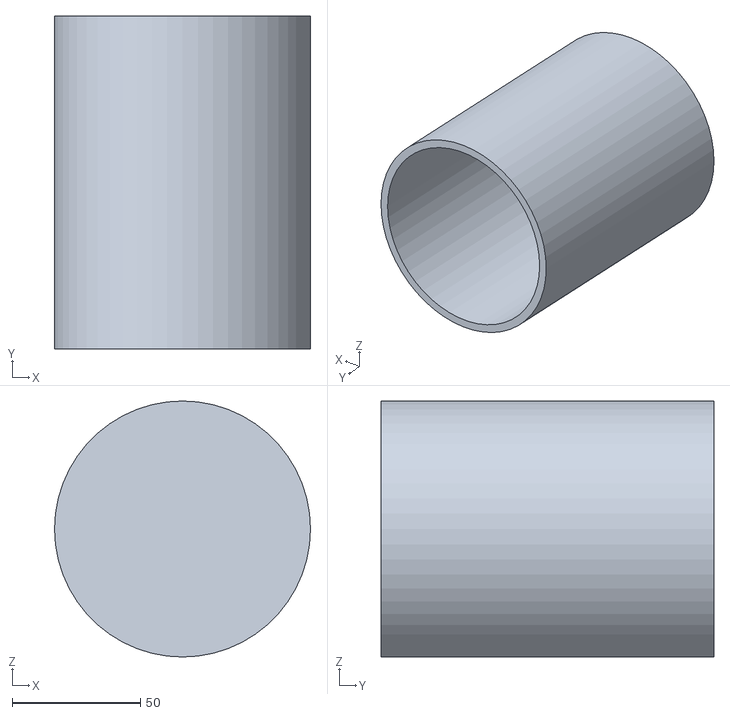
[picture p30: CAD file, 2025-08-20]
ros_navigation/slam_gmapping/stl/huapeng.STL
100.0 x 130.0 x 100.0

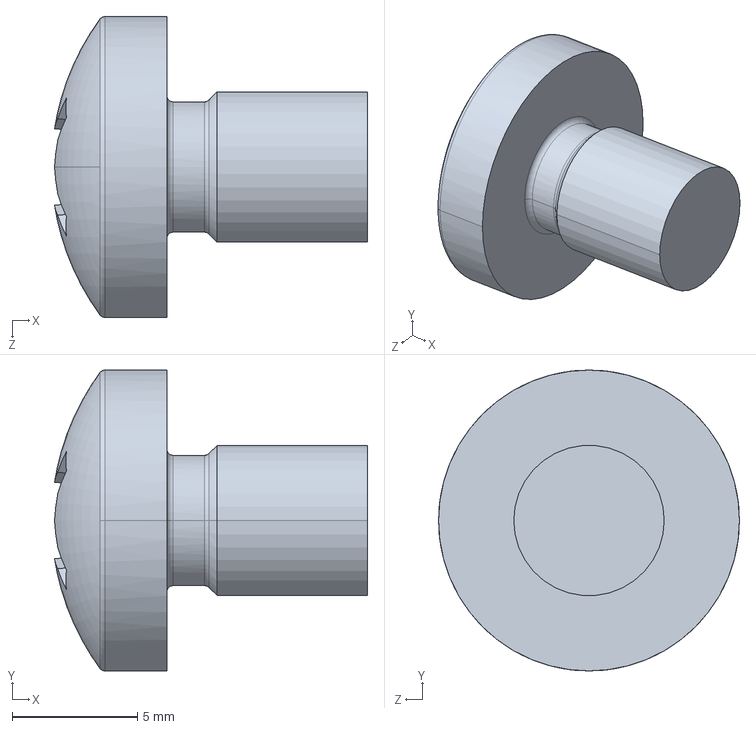
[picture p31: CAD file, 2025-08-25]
结构/连接件/GB╱T 818-2016[十字槽盘头螺钉M6×8].SLDPRT
12.5 x 12.0 x 12.0 mm

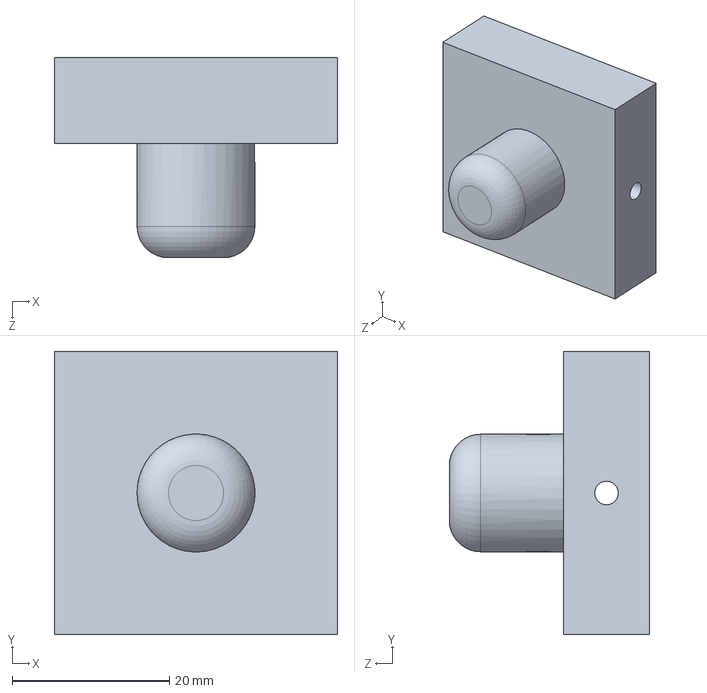
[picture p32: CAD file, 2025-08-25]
结构/零件/相机.SLDPRT
36.0 x 36.0 x 25.5 mm

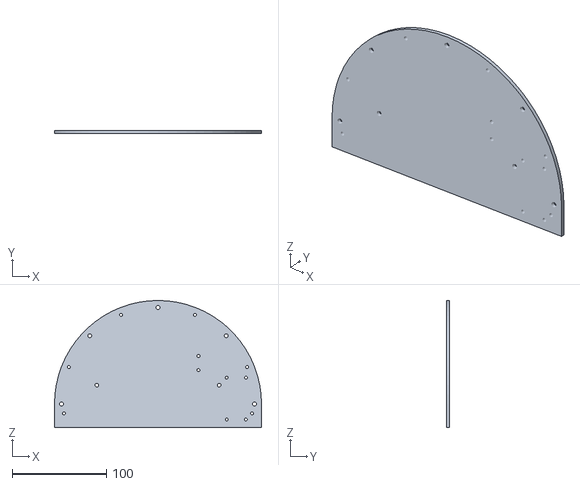
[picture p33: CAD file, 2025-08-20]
ros_navigation/slam_gmapping/stl/zc_1.STL
220.0 x 3.00 x 135.0

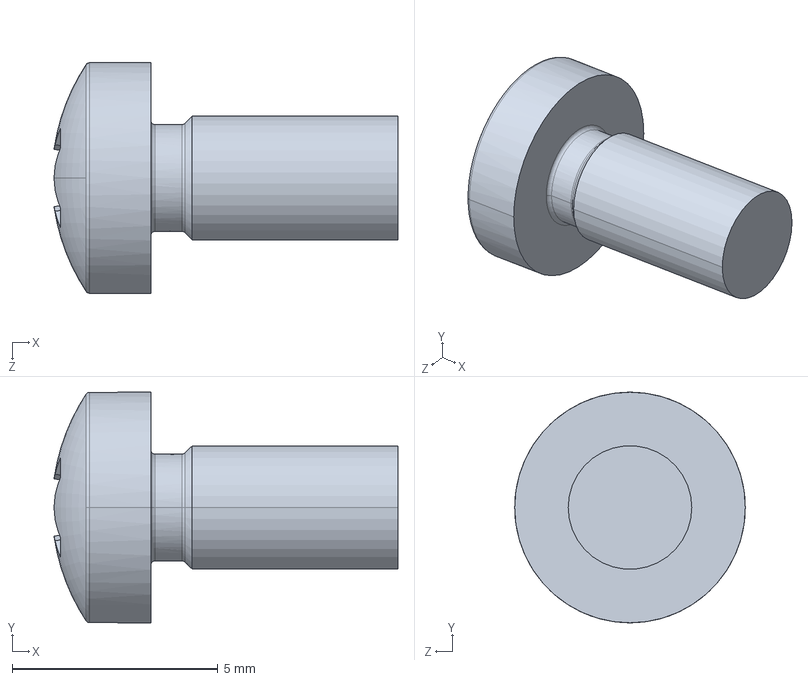
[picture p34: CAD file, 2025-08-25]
结构/连接件/GB╱T 818-2016[十字槽盘头螺钉M3×6].SLDPRT
8.35 x 5.60 x 5.60 mm

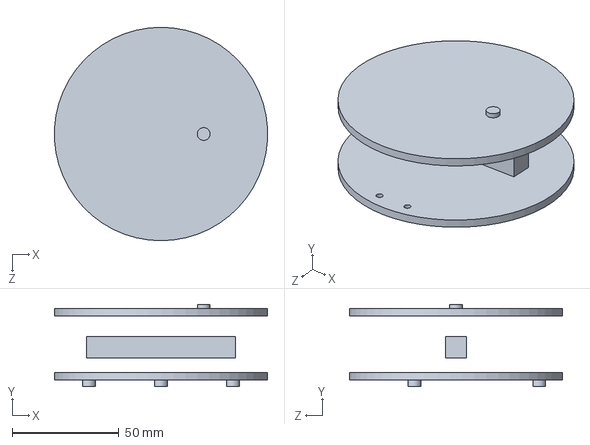
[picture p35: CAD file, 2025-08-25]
结构/零件/压力传感器100.SLDPRT
99.8 x 38.5 x 100.0 mm

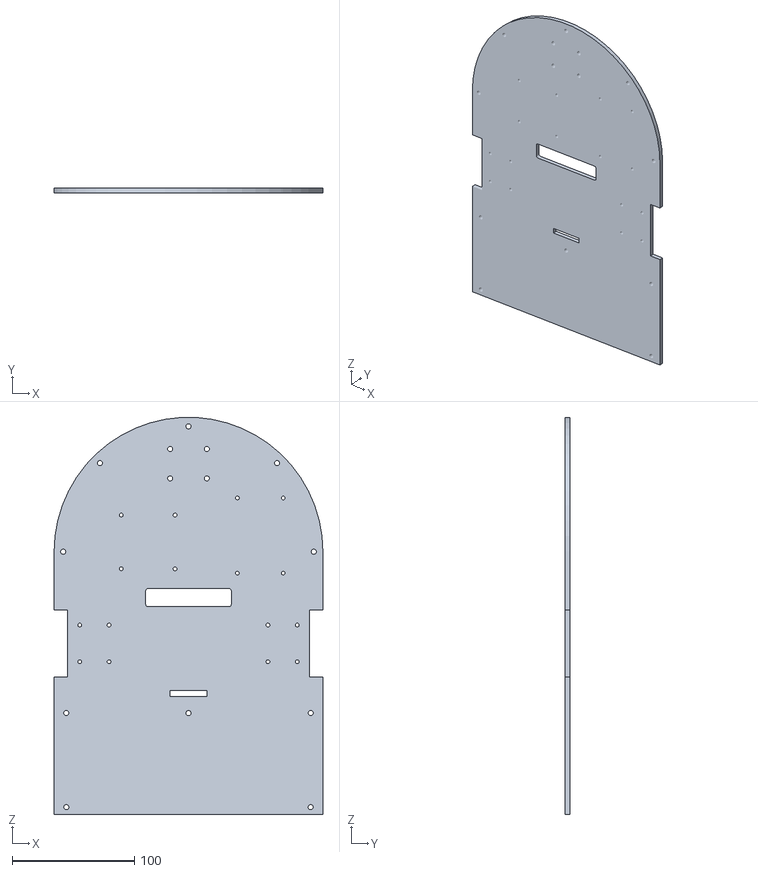
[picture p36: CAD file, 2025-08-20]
ros_navigation/slam_gmapping/stl/dipan.STL
220.0 x 4.00 x 324.8

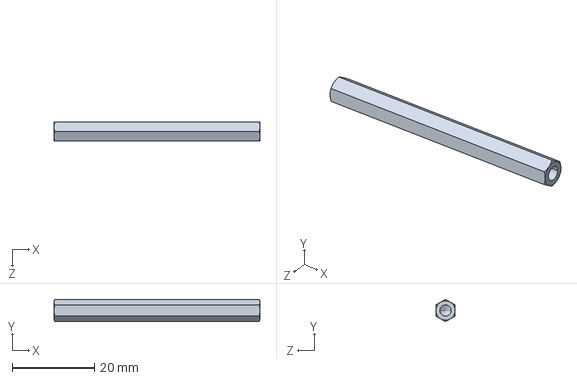
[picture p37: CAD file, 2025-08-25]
结构/连接件/双通六角螺柱M3-L50].sldprt
50.0 x 5.43 x 4.70 mm

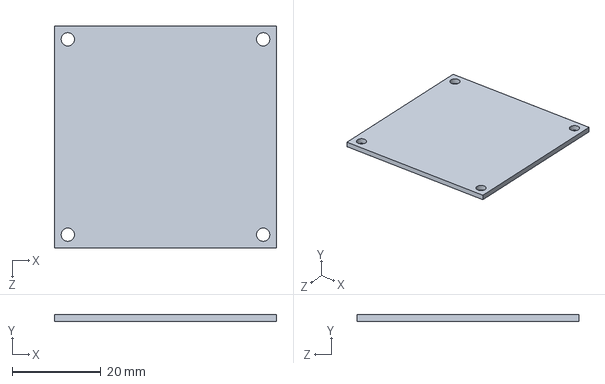
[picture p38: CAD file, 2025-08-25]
结构/零件/tb6612 50×50.SLDPRT
50.0 x 1.50 x 50.0 mm

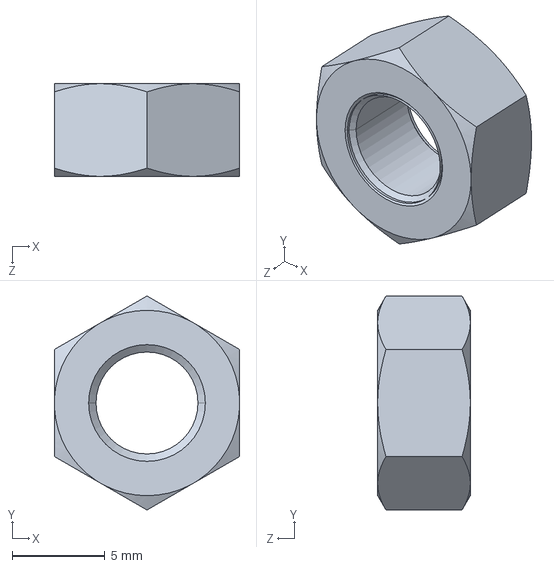
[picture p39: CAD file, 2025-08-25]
结构/连接件/六角螺母 SLMNA[SLMNA-M6].SLDPRT
10.0 x 11.5 x 5.00 mm

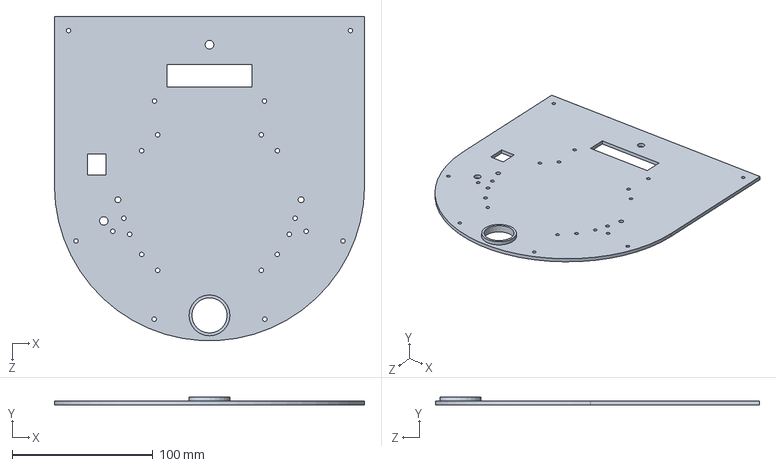
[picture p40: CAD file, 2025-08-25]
结构/零件/支撑件_最顶部.SLDPRT
220.0 x 6.00 x 229.8 mm

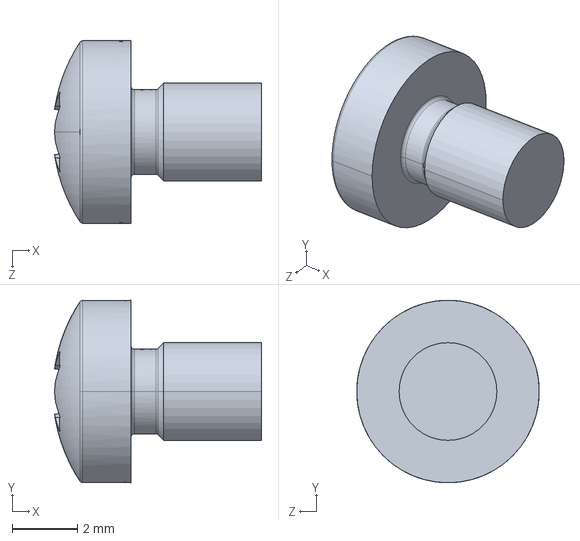
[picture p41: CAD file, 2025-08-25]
结构/连接件/GB╱T 818-2016[十字槽盘头螺钉M3×4].SLDPRT
6.35 x 5.60 x 5.60 mm

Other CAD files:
结构/零件/花盆支撑.SLDPRT
结构/连接件/GB╱T 818-2016[十字槽盘头螺钉M3×10].SLDPRT
结构/零件/支撑件_最底部.SLDPRT
结构/连接件/GB╱T 818-2016[十字槽盘头螺钉M2×6].SLDPRT
结构/连接件/GB╱T 818-2000[十字槽盘头螺钉M4×6].SLDPRT
结构/连接件/GB╱T 818-2016[十字槽盘头螺钉M3×8].SLDPRT
结构/连接件/GB╱T 818-2016[十字槽盘头螺钉M4×8].SLDPRT
结构/连接件/六角螺母 SLMNA[SLMNA-M3].SLDPRT
结构/连接件/单通六角螺柱M3-L5].SLDPRT
结构/连接件/双通六角螺柱M3-L25].SLDPRT
结构/连接件/双通六角螺柱M4-L16].SLDPRT
结构/连接件/双通六角螺柱M4-L30].SLDPRT
结构/连接件/双通六角螺柱M4-L60].SLDPRT
结构/零件/0.96寸led大概.SLDPRT
结构/零件/1寸万向轮(30X24).SLDPRT
结构/零件/6490开发板100×130×39.25.SLDPRT
结构/零件/E351S电池.SLDPRT
结构/零件/MG513P3012V电机.SLDPRT
结构/零件/MG513电机支架.SLDPRT
结构/零件/stm32开发板51_2×82_8.SLDPRT
结构/零件/一体化麦.SLDPRT
结构/零件/上层竖直安装版.SLDPRT
结构/零件/底架.SLDPRT
结构/零件/引导平台.SLDPRT
结构/零件/支撑件_上部.SLDPRT
结构/零件/相机支架.SLDPRT
结构/零件/稳压电源模块.SLDPRT
结构/零件/继电器50x25x18.5.SLDPRT
结构/零件/花盆100×100×130.SLDPRT
结构/零件/花盆引导架.SLDPRT
结构/零件/蓄水容器.SLDPRT
结构/零件/蓄水容器盖子.SLDPRT
结构/零件/蠕动泵.SLDPRT
结构/零件/雷达.SLDPRT

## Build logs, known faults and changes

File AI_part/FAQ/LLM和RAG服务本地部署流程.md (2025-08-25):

# LLM服务本地部署

#### 1、下载软件工具

```shell
# 下载 aidllm 安装包
	wget https://aidllm.aidlux.com/files/aidllm_2.0.0_arm64.aid.gpg

# 安装 aidllm
	sudo aid-pkg -i -d aidllm_2.0.0_arm64.aid.gpg

# 下载 aidgen-sdk 安装包
	wget http://192.168.110.22:18080/job/aplux_aidgen/9/artifact/aidgen-sdk_1.0.0.9_arm64_ub2204.aid.gpg

# 安装 aidgen-sdk🔍 查询可⽤模型
	sudo aid-pkg -i -d aidgen-sdk_1.0.0.9_arm64_ub2204.aid.gpg

# 下载 aid-open-api 安装包
	wget https://aidllm.aidlux.com/files/aid-openai-api_2.0.0_arm64.aid.gpg

# 安装 aid-openao-api
	sudo aid-pkg -i -d aid-openai-api_2.0.0_arm64.aid.gpg
```

### 2、部署下载的模型

```shell
# 查看远程支持的模型
aidllm remote-list api
    Current Soc : 8550
    Name Url CreateTime
    
# 拉去远程模型
aidllm pull api aplux/aplux_qwen2.5-3B

# 查看本地已下载模型列表
	aidllm list api

# 加载模型
	aidllm start api -m aplux_qwen2.5-3B

# 安装 UI 前端服务
	sudo aidllm install ui
	sudo aidllm start ui
```

### 3、部署模型的文件结构

✅ **GGUF** 类型模型（跨平台⽀持，推荐模型格式）

###### 	路径：/opt/aidlux/app/aid-openai-api/res/models/qwen2.5-1.5b-instruct-q4_k_m/qwen2.5-1.5b-instruct-q4_k_m.gguf

```shell
推荐⽂件结构如下：
    qwen2.5-1.5b-instruct-q4_k_m/
        ├── qwen2.5-1.5b-instruct-q4_k_m.gguf
        ├── qwen2.5-1.5b-instruct-q4_k_m.json ← 模型配置文件（需手动编写）    
json配置⽂件模板：
{
    "backend_type": "llamacpp",
        "model": {
        	"path": "<模型文件绝对路径>"
        }
}
```

### 4、**Linux** 系统模型上传步骤：

#### **1.** 上传整个模型⽬录（包含多个权重或配置⽂件）

```shell
	scp -r /local/path/to/qwen2.5-1.5b-instruct-q4_k_m user@linux-device-ip:/opt/aidlux/app/aidopen-api/res/models/
```

#### **2.** 本地拷⻉⽅式

```shell
	cp -r qwen2.5-1.5b-instruct-q4_k_m /opt/aidlux/app/aid-open-api/res/models/
```

#### **3.** 将上传的模型⽂件加⼊**aidllm**配置

##### 	1. 打开aidllm的api_cfg.json配置⽂件

```shell
	vim /opt/aidlux/app/aid-openai-api/api-cfg.json
	
	结构内容如下：
	{
        "prompt_template_list":[
            {"qwen1.5":"<|im_start|>system\n{0}<|im_end|>\n<|im_start|>user\n{1}<|im_end|>\n<|im_start|>assistant\n"},
            {"qwen2":"<|im_start|>system\n{0}<|im_end|>\n<|im_start|>user\n{1}<|im_end|>\n<|im_start|>assistant\n"},
            {"deepseek":"<｜begin▁of▁sentence｜>{0}<｜User｜>{1}<｜Assistant｜>"}
        ],
        "model_cfg_list":[
             {
              "model_id": "Qwen3-0.6B-Q8_gguf",
              "model_create": "1750843418159",
              "model_owner": "aplux",
              "cfg_path": "./models/Qwen3-0.6B-Q8_gguf/Qwen3-0.6B-Q8_gguf.json",
              "prompt_template_type": "qwen2"
            }
        ],
        "http_cfg":[
            {"ip":"0.0.0.0"},
            {"port":8888}
        ],
        "work_folder":"/opt/aidlux/app/aid-openai-api",
        "dsp_skel_folder":"",
        "res_folder":"./res",
        "log_level" : "INFO",
        "log_folder" : "./logs/",
        "default_model_id": ""
    }
```

##### 	2.在**model_cfg_list**列表⼿动修改，添加模型配置信息

```shell
字段说明：
model_id ：模型标识，唯⼀ ID，⽤于运⾏时指定模型，例如 qwen2.5-1.5b-instruct-q4_k_m 。

model_create ：模型注册时间戳，可使⽤命令 printf "%s%03d\n" "$(date +%s)" "$((10#$(date +%N)/ 1000000))" ⽣成，单位为毫秒。

model_owner ：模型所有者名称，可⾃定义，例如 "aplux" 。

cfg_path ：模型主配置⽂件路径，Linux 下使⽤相对路径（如 ./models/... ），Android 下需使⽤绝对路径（如 /sdcard/... ）。
		./models/qwen2.5-1.5b-instruct-q4_k_m/qwen2.5-1.5b-instruct-q4_k_m.json
		./models/qwen2.5-1.5B-instruct-8550-bin/qwen2.5-1.5b-instruct-htp.json
		注意一点为添加bin类型模型配置文件时，需要指定例如：qwen2.5-1.5b-instruct-htp.json，而非htp-backend.json

prompt_template_type ：对话提⽰模板类型，常⻅取值如 "qwen1.5" 、 "qwen2" 、 "deepseek" ，应与模型训练格式匹配。

```

##### 	4.使⽤ **aidllm** 命令⾏⼯具查看添加模型

```shell
# 使用aidllm list api命令查看模型是否已经加入aidllm
    aidllm list api
        qwen2.5-7b-instruct
        aplux_qwen2-7B
        qwen2.5-7b-instruct-q4_k_m
        qwen2.5-7B-8550
        qwen2.5-1.5b-instruct-q4_k_m
        qwen2.5-1.5B-instruct-8550-bin

# 使用aidllm start api -m qwen2.5-1.5b-instruct-q4_k_m 指定运行模型，查看模型是否能够运行
    aidllm start api -m qwen2.5-1.5b-instruct-q4_k_m
```

## 知识库RAG（Retrieval-Augmented Generation）服务本地部署

### 1、安装软件工具包

```shell
# 下载 aidllm 安装包
	wget https://aidllm.aidlux.com/files/aidllm_2.0.0_arm64.aid.gpg

# 安装 aidllm
	sudo aid-pkg -i -d aidllm_2.0.0_arm64.aid.gpg

# 下载 aidgen-sdk 安装包
	wget http://192.168.110.22:18080/job/aplux_aidgen/9/artifact/aidgen-sdk_1.0.0.9_arm64_ub2204.aid.gpg
	
# 安装 aidgen-sdk
	sudo aid-pkg -i -d aidgen-sdk_1.0.0.9_arm64_ub2204.aid.gpg
```

### 2、获取aidlux账号

🔐一、注册账号

访问 aidlux（[Profile | AidLux Single Sign-On](https://auth.aidlux.com/zh/user/profile)） 官⽹，注册并登录⼀个 **Aidlux** 账号。

📚 ⼆、创建 **RAG** 知识库

   1.🌐 登录 **aidllm-cms**

	打开浏览器访问 👉 https://aidllm.aidlux.com，使⽤你的 Aidlux 账号登录

   2.🧭 进⼊知识库管理界⾯

	登录后点击左侧“知识库”菜单，进⼊管理⻚⾯，点击“新建”。

    3.📝 填写知识库信息

	名称：仅⽀持英⽂字⺟和数字（如： MyRAG2025 ）。

	嵌⼊模型：选择当前已加载的 embedding 模型。

	切⽚⽅法：可选 General 或 Q&A ，具体说明如下：

🧩 切⽚⽅法 	📄 ⽀持格式 		📖 说明

General		⽂本（.txt /.pdf）	将连续⽂本按“分段标识符”分割，再按Token 数量不超过“最⼤⻓度”合并为⼀块。

Q&A			.xlsx / .csv /.txt	  ⽤于问答格式：Excel 两列（⽆表头：问题 / 答案）；CSV / TXT 使⽤ **Tab** 分隔，UTF-8 编码。

💻 三、命令⾏操作 **aidllm**

1. 🔑 登录远程 **cms**

```shell
	aidllm login
```

2. 安装RAG服务

   ```
   sudo aidllm install rag
   ```

3. 📃 查看知识库列表

   ```shell
   aidllm remote-list rag
   
       Name EmbeddingModel CreateTime
       aidluxdocs BAAI/bge-large-zh-v1.5 2025-07-09 14:56:31
   ```

4. 拉取知识库和启动

   ```shell
   aidllm pull rag <知识库名称>
   aidllm start rag
   aidllm start rag -n <知识库名称>
   ```

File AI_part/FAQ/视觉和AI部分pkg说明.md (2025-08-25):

## pkg 说明

##### <span style="color:red">数据可能没有同步，但是参数类型是这些，详细数据源码</span>

### 1、camera_start_python：相机驱动包

##### 	cam_pub.py : 打开相机，并发布原始图像话题 

```python
        -node名称:aidlux_camera_publisher
        -/camera/image_raw : topic:
            -pub
            -FPS：10
            -图像宽Width=1280
            -图像高Height=720
```

##### 方法使用：

```sh
1、切换到root用户
2、ros2 run camera_start_python cam_pub运行节点
```

### 2、yolov5_check:yolov5功能部分

##### 	yolov5_check.py：检测图片人物

```python
        -node名称:yolo_detector_node 
        -/camera/image_raw:topic:  
            -sub
            -FPS:：10
        -/person_detection:topic:
            -pub
            -type:PointStamped(坐标点x,y,z类型)
            -FPS:10
        -/yolo_result_image:topic:
            -pub
            -type:Image
            -FPS:10
        -/start_yolo:server:
            -service
            -type:std_srvs/SetBool(bool处理服务)
```

##### 	qnn_yolov5_multi.py：yolo检测模块

```python
   -YOLO_Detector : Class ：yolo检测类
   		-__init__(self,model_name,resource_dir):创建对象输入两个参数
     	-Detect ： 嵌入Class ：yolo检测头，处理模型输出并生成检测结果
  		-yolo_detect(self,input_frame)：function : 对图像输入处理，yolo检测，输出目标框box
```

##### 方法使用：

        1、切换到root用户
        2、执行 python src/yolov5_check/yolov5_check/yolov5_check.py 启动节点
    	3、使用 ros2 service call /start_yolo std_srvs/srv/SetBool "{data: true}" 向节点服务端发送请求，开启yolo检测节点，并改变寄存器 bit 标志位为1
    	4、使用 ros2 run camera_start_python cam_pub 开启相机节点
    	5、使用 ros2 service call /start_yolo std_srvs/srv/SetBool "{data: false}" 向节点服务端发送请求，关闭yolo检测节点，并改变寄存器 bit 标志位为0

### 3、robot_core:机器人公共包，仅仅只是提供操作的class，不实现任何实际功能

#####     -robot_core.py：机器人功能模块，将机器人整体状态放在一个int中

```python
        -bit_enum : Class : 机器人状态bit枚举类
    	"""	（按照优先级排序，数字越小，优先级越高） """
            -SLAM_bit = 0 :第0位，SLAM建图是否完成
        -my_robot_state : Object : 机器人状态实例对象
            -get_int() : function : 获取机器人状态int
            -set_int(int) : function : 设置机器人状态int
            -set_bit(bit_pos : bit_enum, value : bool) : function : 设置机器人状态bit
            -get_bit(bit_pos : bit_enum) : function : 获取机器人状态bit
```

#####     robot_core使用方法：

```python
        1、robot_core是一个软件包将其放在src/下
        2、在需要使用的软件包的package.xml中，加上依赖robot_core包，如：
            <depend>robot_core</depend>
        3、引入机器人状态实例
            from robot_core.robot_state import my_robot_state    
        4、直接对 my_robot_state 操作，或者将其引用到你的类中 self.my_robot_state = my_robot_state
```

### 4、voice_interaction：AI中关键字唤醒、ASR、LLM、STT模块

##### -vadrecorder_node.py:关键字唤醒和音频读取功能

```python
	-AudioStreamManager： Class : 音频流控制，实现音频对象的处理
    -node名称:vad_wake_node 
        -vad/start:topic: 关键字唤醒之后，向调节节点发布vad开始 
            -sub
            -type:Bool
            -FPS:：10
        -wake_word/reset:topic: 来自调节节点，重置关键字唤醒
            -sub
            -type:Bool
            -FPS:：10
        -audio/raw_wav:topic:向asr发送音频信息
            -pub
            -type:Float32MultiArray(音频流数据类型)
            -FPS:10
        -wake_word/detected:topic:关键字唤醒确认
            -pub
            -type:Bool
            -FPS:10
```

##### -等其它文件包

#### 命令行备份

1、ros2 launch voice_interaction voice_interaction_launch.py 

2、ros2 service call /start_AI std_srvs/srv/SetBool "{data: "True"}"

3、htop

4、ros2 topic pub --once /asr/result std_msgs/msg/String "{data: 'Hello，为什么植物会变黄'}"

### 知识库下载安装

1、先按照AI安装流程安装

2、启动模型api

2、 安装 UI 服务

	aidllm install ui

3、注册和登录aidlux 账号

4、安装rag

	aidllm install rag

5、查看可⽤向量知识库

	aidllm remote-list rag

6、下载指定数据库

	aidllm pull rag tesla

	列出本地数据库

	aidllm list rag

7、开启三个服务

	aidllm start api -m <model_name> # 指定模型启动

	aidllm start ui

	aidllm start rag -n tesla # 启动指定知识库

8、[localhost:51104](http://192.168.110.61:51104/)是AI的ui接口



**http://<**本机**IP>:18111/docs**是知识库接口的docs请求回应说明



	开启rag服务之后，使用python申请<本机IP>：18111的请求可以得到response

##### 9、所有的 api \ rag \ ui 配置文件都在 /opt/aidlux/app 下面

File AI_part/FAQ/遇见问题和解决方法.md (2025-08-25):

##### 1、web 8000端口的各种应用不连接

```bash
#重启服务
sudo nginx
```

##### 2、web端 ubuntu Desktop 不在桌面上，在web端更新Aid-Desktop软件即可

##### 3、使用QC6490开发板遇到的问题

```shell
1、文档中刷机完后下载各种软件使用的是有线网，但是还可以使用电脑或者手机连接上APLUXwifi之后再打开热点，将板子、手机、电脑在一个热点下面，这样就是基于APLUX的局域网，也在APLUX内网下，可以减少有线网连接

--- 下载文件时最好使用有线网，更加稳定和快速。目前板子的有线网口还存在问题，正在解决中：1、左边网口即eth0 的mac地址是写死了的，所有板子都是同一个mac。因此大家在使用时会导致IP冲突。 2、右边网口即eth1的mac是随机的，即每个板子每次重启都会随机生成一个mac，就会导致IP地址发生变化。 如果你们想用稳定的ip地址，可以尝试使用wifi连接。可以直接找刘维斌看能否给大家申请天线，就可以直接连接APLUX网络了。

2、板子的VNC服务不稳定，不知道什么原因，有的是拒绝，有的是超时，暂时不知道原因。Web8000端口也是只能被动显示（比如代码中的cv.imshow），不可以主动显示，比如不能打开rviz2，报错没有显示器。可以使用Xshell套装，盗版或者是30天免费使用就可以，基于ssh的主动显示。
 另外方法：ros2使用的是tcp通信，可以使用linux系统连接那个节点，但是需要路由器带动带宽

---vnc连接不稳定应该跟网络有关，如连接的wifi，可能导致网络不稳当，vnc就会断开。 Web8000上确认是不能打开rviz2的；可通过xshell、mobaxterm（有免费社区版）等调用本地资源打开。

3、ubuntu系统中使用设备权限问题，在ubuntu中使用设备需要加上sudo命令，一旦涉及到硬件（目前发现是usb耳机音响），如果仅仅是查看设备信息，有些都需要sudo

--当前系统默认进入的都是aidlux用户，它仅在/home/aidlux目录下有操作权限。一些系统命令或者去其他目录下操作都应当加sudo的。没有问题。

4、板子有时不知道为什么直接断电，可能是死机原因

--更换为最新固件，蓝灯版本

5、Aidlux的所有软件拒绝连接，比如终端、应用中心等

--sudo nginx重启一下服务

6、VNC中打开VS Code 在尝试创建沙盒环境时遇到了权限问题（Operation not permitted），通常与 Linux 系统的命名空间（namespace）限制或安全策略有关。以下是解决方案：

 禁用沙盒模式（推荐）

直接运行以下命令绕过沙盒检查：

/usr/share/code/bin/code --no-sandbox --user-data-dir=~/.vscode-unsandboxed
```

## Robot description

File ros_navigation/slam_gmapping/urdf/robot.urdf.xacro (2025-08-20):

<?xml version="1.0"?>
<robot xmlns:xacro="http://www.ros.org/wiki/xacro" name="first_robot">

    <!-- ?????????0.5 ??????????????? -->
    <xacro:property name="scale" value="1.0" />

    <!-- Base Footprint -->

    <!-- Base Link -->
    <link name="base_link">
        <visual>
            <origin xyz="0.0 0.0 0.0" rpy="0.0 0.0 0.0"/>
            <geometry>
                <box size="${0.33*scale} ${0.22*scale} ${0.062*scale}"/>
            </geometry>
            <material name="red">
                <color rgba="1.0 0.0 0.0 0.5"/>
            </material>
        </visual>
    </link>

    <!-- SC Base Link -->
    <link name="sc_base_link">
        <visual>
            <origin xyz="0.0 0.0 0.0" rpy="0.0 0.0 0.0"/>
            <geometry>
                <box size="0.23 0.22 0.049"/>
            </geometry>
            <material name="blue">
                <color rgba="0.3 0.2 0.5 0.7"/>
            </material>
        </visual>
    </link>

    <!-- HP Link (Cylinder) -->
    <link name="hp_link">
        <visual>
            <origin xyz="0.0 0.0 0.0" rpy="0.0 0.0 0.0"/>
            <geometry>
                <cylinder radius="${0.05*scale}" length="${0.1*scale}"/>
            </geometry>
            <material name="white">
                <color rgba="1.0 1.0 1.0 0.5"/>
            </material>
        </visual>
    </link>

    <!-- Laser Support Link -->
    <link name="lase_support_link">
        <visual>
            <origin xyz="0.0 0.0 0.0" rpy="0.0 0.0 0.0"/>
            <geometry>
                <box size="${0.005*scale} ${0.005*scale} ${0.03*scale}"/>
            </geometry>
            <material name="red">
                <color rgba="1.0 0.0 0.0 1.0"/>
            </material>
        </visual>
    </link>

    <!-- Laser Link -->
    <link name="laser">
        <visual>
            <origin xyz="0.0 0.0 0.0" rpy="0.0 0.0 0.0"/>
            <geometry>
                <cylinder radius="${0.03*scale}" length="${0.02*scale}"/>
            </geometry>
            <material name="yallow">
                <color rgba="1.0 1.0 0.0 0.5"/>
            </material>
        </visual>
    </link>

    <!-- Wheels (Left and Right) -->
    <link name="zuo_wheel_link">
        <visual>
            <origin xyz="0.0 0.0 0.0" rpy="-1.57 0.0 0.0"/>
            <geometry>
                <cylinder radius="${0.03*scale}" length="${0.02*scale}"/>
            </geometry>
            <material name="white">
                <color rgba="1.0 1.0 1.0 0.5"/>
            </material>
        </visual>
    </link>

    <link name="you_wheel_link">
        <visual>
            <origin xyz="0.0 0.0 0.0" rpy="-1.57 0.0 0.0"/>
            <geometry>
                <cylinder radius="${0.03*scale}" length="${0.02*scale}"/>
            </geometry>
            <material name="white">
                <color rgba="1.0 1.0 1.0 0.5"/>
            </material>
        </visual>
    </link>

    <!-- Front Caster Wheel -->
    <link name="qian_caster">
        <visual>
            <origin xyz="0.0 0.0 0.0" rpy="0.0 0.0 0.0"/>
            <geometry>
                <sphere radius="${0.02*scale}"/>
            </geometry>
            <material name="white">
                <color rgba="1.0 1.0 1.0 1.0"/>
            </material>
        </visual>
    </link>

    <!-- Joints (????????) -->


    <joint name="caster_link" type="fixed">
        <origin xyz="-0.15 0.0 -0.05" rpy="0.0 0.0 0.0"/>
        <axis xyz="0.0 0.0 0.0"/>
        <parent link="base_link"/>
        <child link="qian_caster"/>
    </joint>

    <joint name="right_wheel_joint" type="continuous">
        <origin xyz="0.03 0.11 -0.03" rpy="0.0 0.0 0.0"/>
        <axis xyz="0.0 1.0 0.0"/>
        <parent link="base_link"/>
        <child link="you_wheel_link"/>
    </joint>

    <joint name="left_wheel_joint" type="continuous">
        <origin xyz="0.03 -0.12 -0.03" rpy="0.0 0.0 0.0"/>
        <axis xyz="0.0 1.0 0.0"/>
        <parent link="base_link"/>
        <child link="zuo_wheel_link"/>
    </joint>

    <joint name="laser_joint" type="fixed">
        <origin xyz="0.0 0.0 ${0.01*scale}" rpy="0.0 0.0 0.0"/>
        <axis xyz="0.0 0.0 0.0"/>
        <parent link="lase_support_link"/>
        <child link="laser"/>
    </joint>

    <joint name="lase_link_joint" type="fixed">
        <origin xyz="0.12 0.0 0.04" rpy="0.0 0.0 0.0"/>
        <axis xyz="0.0 0.0 0.0"/>
        <parent link="base_link"/>
        <child link="lase_support_link"/>
    </joint>

    <joint name="hs_joint" type="fixed">
        <origin xyz="-0.03 0.0 0.07" rpy="0.0 0.0 0.0"/>
        <parent link="sc_base_link"/>
        <child link="hp_link"/>
        <axis xyz="0.0 0.0 0.0"/>
    </joint>

    <joint name="base_joint" type="fixed">
        <parent link="base_link"/>
        <child link="sc_base_link"/>
        <origin xyz="-0.05 0.0 0.05" rpy="0.0 0.0 0.0"/>
        <axis xyz="0 0 0"/>
    </joint>

</robot>

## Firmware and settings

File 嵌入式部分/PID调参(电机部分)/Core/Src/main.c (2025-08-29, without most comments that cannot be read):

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
/* Includes ------------------------------------------------------------------*/
#include "main.h"
#include "cmsis_os.h"
#include "adc.h"
#include "i2c.h"
#include "tim.h"
#include "usart.h"
#include "gpio.h"

/* USER CODE BEGIN Includes */

#include <stdio.h>
#include "motor_control.h"
#include <string.h>
#include <stdlib.h>
#include "serial_command.h"
#include "../../dht11.h"
#include "motor_control.h"
#include "oled.h"

extern TIM_HandleTypeDef htim1;  
void delay_us_TIM1(uint16_t us);
void delay_ms_TIM1(uint16_t ms);


/* USER CODE END Includes */

/* USER CODE BEGIN PD */
extern uint8_t rx_data;  // 声明外部变量
extern uint8_t ble_rx_data;

/* USER CODE END PD */


void SystemClock_Config(void);
void MX_FREERTOS_Init(void);
/* USER CODE BEGIN 0 */
#include "../../delay.h"
#include "../../ble.h"
#include "../../DFRobot.h"
#include "../../bsp_hx711.h"
#include "../../ds18b20.h"
#include <string.h>

/**
  * @brief  获取土壤湿度百分比（0~100%�?
  * @note   ADC值与湿度成反比，需反向计算
  */
float Get_Soil_Humidity(uint32_t adc_value) {

    if (adc_value >= AIR_VALUE) return 0.0f;
    if (adc_value <= WATER_VALUE) return 100.0f;
    

    return 100.0f * (AIR_VALUE - adc_value) / (AIR_VALUE - WATER_VALUE);
}

/**
  * @brief  根据湿度百分比返回状�?
  */
const char* Get_Humidity_Status(float humidity) {
    if (humidity > 66.0f) return "Very Wet";
    else if (humidity > 33.0f) return "Wet";
    else return "Dry";
}



/* USER CODE END 0 */

/**
  * @brief  The application entry point.
  * @retval int
  */
int main(void)
{

  /* USER CODE BEGIN 1 */
		

	
		/*PlayAnimation_Namal();
		PlayAnimation_Sad();
		PlayAnimation_Adore(); */
	
	
  /* USER CODE END 1 */

  /* MCU Configuration--------------------------------------------------------*/

  /* Reset of all peripherals, Initializes the Flash interface and the Systick. */
  HAL_Init();

  /* Configure the system clock */
  SystemClock_Config();

  /* Initialize all configured peripherals */
  MX_GPIO_Init();
  MX_TIM1_Init();
  MX_USART1_UART_Init();
  MX_USART2_UART_Init();
  MX_TIM2_Init();
  MX_TIM3_Init();
  MX_TIM4_Init();
  MX_USART3_UART_Init();
  MX_ADC1_Init();
  MX_I2C1_Init();
  MX_I2C2_Init();
  MX_I2C3_Init();
  /* USER CODE BEGIN 2 */
  Motor_Init();
	SerialCommand_Init();




    
    // ³õʼ»¯HX711
    Init_HX711pin();
    
    // 获取毛皮重量（去皮）
    Get_Maopi();
//		
//			 		DS18B20_Init();             // ?????DS18B20
//   DS18B20_Start();               // ?????????
//		 if (DS18B20_Init()) {
//        printf("DS18B20 Not Found!\r\n");
//    }
//    printf("DS18B20 Ready on PB15!\r\n");
//	
//    printf("System Initialized\r\n");
//    printf("HX711 Weight Measurement Demo\r\n");

//		int16_t temp_1 = DS18B20_GetTemp();
//    printf("Temperature: %.1f 度 \r\n", temp_1 / 10.0);



  /* USER CODE END 2 */

  /* Init scheduler */
  osKernelInitialize();

  /* Call init function for freertos objects (in cmsis_os2.c) */
  MX_FREERTOS_Init();

  /* Start scheduler */
  osKernelStart();

  /* We should never get here as control is now taken by the scheduler */

  /* Infinite loop */
  /* USER CODE BEGIN WHILE */
   // 初始化OLED
   OLED_Init();
   OLED_Clear(); // 清屏
   
   /* 第一屏显示 */
   // 显示第一行：记录
	 

   
   // 显示第二行：2025年7月23日
//   OLED_ShowNum(0, 2, 2025, 4, 16);  // 年份
//   OLED_ShowCHinese(32, 2, 2);       // "年"
//   OLED_ShowNum(48, 2, 7, 2, 16);    // 月份
//   OLED_ShowCHinese(64, 2, 3);       // "月"
//   OLED_ShowNum(80, 2, 23, 2, 16);   // 日期
//   OLED_ShowCHinese(96, 2, 4);       // "日"
//   
//   // 显示第三行：Hello World!
//   OLED_ShowString(0, 6, "Hello World!", 12);
//   
//   // 保持显示1秒
//   HAL_Delay(1000);
//   
//   /* 第二屏显示 */
//   OLED_Clear(); // 清屏  
//   OLED_ShowCHinese(0,  0, 5); // "团" 
//   OLED_ShowCHinese(16, 0, 6); // "对"
//   OLED_ShowCHinese(32, 0, 7); // "成"
//   OLED_ShowCHinese(48, 0, 8); // "员"
//	 OLED_ShowCHinese(32,4, 9); // "团" 
//   OLED_ShowCHinese(48,4, 10); // "对"
//   OLED_ShowCHinese(64,4, 11); // "成"
//	    // 保持显示1秒
//   HAL_Delay(1000);
//   OLED_Clear(); // 清屏
//	 OLED_ShowCHinese(0,  0, 5); // "团" 
//   OLED_ShowCHinese(16, 0, 6); // "对"
//   OLED_ShowCHinese(32, 0, 7); // "成"
//   OLED_ShowCHinese(48, 0, 8); // "员"
//	 OLED_ShowCHinese(32,4, 12); // "团" 
//   OLED_ShowCHinese(48,4, 13); // "对"
//   OLED_ShowCHinese(64,4, 14); // "成"
//	    // 保持显示1秒
//   HAL_Delay(1000);
//	 OLED_Clear(); // 清屏
//	 OLED_ShowCHinese(0,  0, 5); // "团" 
//   OLED_ShowCHinese(16, 0, 6); // "对"
//   OLED_ShowCHinese(32, 0, 7); // "成"
//   OLED_ShowCHinese(48, 0, 8); // "员"
//	 OLED_ShowCHinese(32,4, 15); // "团" 
//   OLED_ShowCHinese(48,4, 16); // "对"
//   OLED_ShowCHinese(64,4, 17); // "成"
//	 
//	    HAL_Delay(1000);
//	 OLED_Clear(); // 清屏
//	 OLED_ShowCHinese(0,  0, 5); // "团" 
//   OLED_ShowCHinese(16, 0, 6); // "对"
//   OLED_ShowCHinese(32, 0, 7); // "成"
//   OLED_ShowCHinese(48, 0, 8); // "员"
//	 OLED_ShowCHinese(48,4, 18); // "团" 
//   OLED_ShowCHinese(64,4, 19); // "对"

//	    HAL_Delay(1000);
//	 OLED_Clear(); // 清屏
//	 OLED_ShowCHinese(0,  0, 5); // "团" 
//   OLED_ShowCHinese(16, 0, 6); // "对"
//   OLED_ShowCHinese(32, 0, 7); // "成"
//   OLED_ShowCHinese(48, 0, 8); // "员"
//	 OLED_ShowCHinese(32,4, 20); // "团" 
//   OLED_ShowCHinese(48,4, 21); // "对"
//   OLED_ShowCHinese(64,4, 22); // "成"
//	    HAL_Delay(1000);
//	 OLED_Clear(); // 清屏
//	 OLED_ShowCHinese(0,  0, 5); // "团" 
//   OLED_ShowCHinese(16, 0, 6); // "对"
//   OLED_ShowCHinese(32, 0, 7); // "成"
//   OLED_ShowCHinese(48, 0, 8); // "员"
//	 OLED_ShowCHinese(48,4, 23); // "团" 
//   OLED_ShowCHinese(64,4, 24); // "对"

//	    HAL_Delay(1000);
//	 OLED_Clear(); // 清屏
//	 OLED_ShowCHinese(0,  0, 5); // "团" 
//   OLED_ShowCHinese(16, 0, 6); // "对"
//   OLED_ShowCHinese(32, 0, 7); // "成"
//   OLED_ShowCHinese(48, 0, 8); // "员"
//	 OLED_ShowCHinese(32,4, 25); // "团" 
//   OLED_ShowCHinese(48,4, 26); // "对"
//   OLED_ShowCHinese(64,4, 27); // "成"
//	 

  while (1)
  {
//				HAL_GPIO_TogglePin(GPIOC, GPIO_PIN_6);  // 切换PC6引脚电平
//		    HAL_Delay(1000);
//				int16_t temp_1 = DS18B20_GetTemp();
//        printf("Temperature: %.1f度 \r\n", temp_1 / 10.0);
	      // 正转
//        Motor_Set(600, 600, 1, 1);
//        HAL_Delay(5);
//        Motor_UpdateSpeed();
//        // 反转
//        Motor_Set(600, 600, 0, 0);
//        HAL_Delay(5);
//        Motor_UpdateSpeed();

//        Motor_Set(0, 0, 0, 0);
//        HAL_Delay(5);
//        Motor_UpdateSpeed();
    /* USER CODE END WHILE */

    /* USER CODE BEGIN 3 */
//				Get_Weight();        
//        // 使用Weight_Shiwu获取重量值
//        printf("Current Weight: %d g\r\n", Weight_Shiwu);        
//        HAL_Delay(500);							
//		    HAL_GPIO_TogglePin(GPIOF, GPIO_PIN_9 | GPIO_PIN_10);
//        printf("DHT11 Test Start\r\n");
//        uint8_t temp, humi;				
//				HAL_UART_Receive_IT(&huart2, &ble_rx_data, 1);  
//				printf("System Ready. Waiting for Bluetooth Data...\r\n");		
//					
//				uint32_t moisture = Read_Soil_Moisture();

//        Check_Moisture_Level(moisture);        // 判断湿度等级


//        const char* status = Get_Humidity_Status(humidity);
//        printf("ADC: %lu, Humidity: %.1f%%, Status: %s \r\n", 
//               adc_value, humidity, status);							 
//        HAL_Delay(500);	
  }
  /* USER CODE END 3 */
}

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
/* USER CODE BEGIN 4 */
void HAL_UART_RxCpltCallback(UART_HandleTypeDef *huart)
{
    if (huart->Instance == USART3) {
        SerialCommand_ProcessChar(rx_data);
        HAL_UART_Receive_IT(&huart3, &rx_data, 1);  // 继续接收
    } else if (huart->Instance == USART2) {
        BLE_UART_ReceiveCallback(ble_rx_data);
        HAL_UART_Receive_IT(&huart2, &ble_rx_data, 1);  // 继续接收
    }
}

/* USER CODE END 4 */

/**
  * @brief  Period elapsed callback in non blocking mode
  * @note   This function is called  when TIM7 interrupt took place, inside
  * HAL_TIM_IRQHandler(). It makes a direct call to HAL_IncTick() to increment
  * a global variable "uwTick" used as application time base.
  * @param  htim : TIM handle
  * @retval None
  */
void HAL_TIM_PeriodElapsedCallback(TIM_HandleTypeDef *htim)
{
  if (htim->Instance == TIM7)
  {
    HAL_IncTick();
  }
}

/**
  * @brief  This function is executed in case of error occurrence.
  * @retval None
  */
void Error_Handler(void)
{
  /* USER CODE BEGIN Error_Handler_Debug */
  /* User can add his own implementation to report the HAL error return state */
  __disable_irq();
  while (1)
  {
  }
  /* USER CODE END Error_Handler_Debug */
}

#ifdef  USE_FULL_ASSERT
/**
  * @brief  Reports the name of the source file and the source line number
  *         where the assert_param error has occurred.
  * @param  file: pointer to the source file name
  * @param  line: assert_param error line source number
  * @retval None
  */
void assert_failed(uint8_t *file, uint32_t line)
{
  /* USER CODE BEGIN 6 */
  /* User can add his own implementation to report the file name and line number,
     ex: printf("Wrong parameters value: file %s on line %d\r\n", file, line) */
  /* USER CODE END 6 */
}
#endif /* USE_FULL_ASSERT */

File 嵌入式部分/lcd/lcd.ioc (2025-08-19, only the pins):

Mcu.UserName=STM32F407ZGTx
PA13.Signal=SYS_JTMS-SWDIO
PA14.Signal=SYS_JTCK-SWCLK
PC14-OSC32_IN.Signal=RCC_OSC32_IN
PC15-OSC32_OUT.Signal=RCC_OSC32_OUT
PD0.Signal=FSMC_D2_DA2
PD1.Signal=FSMC_D3_DA3
PD10.Signal=FSMC_D15_DA15
PD14.Signal=FSMC_D0_DA0
PD15.Signal=FSMC_D1_DA1
PD4.Signal=FSMC_NOE
PD5.Signal=FSMC_NWE
PD8.Signal=FSMC_D13_DA13
PD9.Signal=FSMC_D14_DA14
PE10.Signal=FSMC_D7_DA7
PE11.Signal=FSMC_D8_DA8
PE12.Signal=FSMC_D9_DA9
PE13.Signal=FSMC_D10_DA10
PE14.Signal=FSMC_D11_DA11
PE15.Signal=FSMC_D12_DA12
PE7.Signal=FSMC_D4_DA4
PE8.Signal=FSMC_D5_DA5
PE9.Signal=FSMC_D6_DA6
PF0.Signal=FSMC_A0
PF1.Signal=FSMC_A1
PF12.Signal=FSMC_A6
PF13.Signal=FSMC_A7
PF14.Signal=FSMC_A8
PF15.Signal=FSMC_A9
PF2.Signal=FSMC_A2
PF3.Signal=FSMC_A3
PF4.Signal=FSMC_A4
PF5.Signal=FSMC_A5
PG0.Signal=FSMC_A10
PG1.Signal=FSMC_A11
PG12.Signal=FSMC_NE4
PG2.Signal=FSMC_A12
PG3.Signal=FSMC_A13
PG4.Signal=FSMC_A14
PG5.Signal=FSMC_A15
PH0-OSC_IN.Signal=RCC_OSC_IN
PH1-OSC_OUT.Signal=RCC_OSC_OUT

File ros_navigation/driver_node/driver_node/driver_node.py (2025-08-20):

import serial
import struct
import rclpy
import threading
from rclpy.node import Node
from geometry_msgs.msg import Twist
from nav_msgs.msg import Odometry
from std_msgs.msg import Float32
from tf2_ros import TransformBroadcaster
from geometry_msgs.msg import TransformStamped, Quaternion
import math
from queue import Queue

class DriveNode(Node):
    def __init__(self):
        super().__init__('drive_node')
        self.declare_parameter('port', '/dev/ttyUSB0')  #  sudo chmod 666 /dev/ttyUSB0 
        # self.declare_parameter('port', '/dev/pts/20')
        self.port = self.get_parameter('port').value

        self.serial_init()

        self.x = 0.0
        self.y = 0.0
        self.th = 0.0
        self.last_recv_time = None
        self.last_cmd = [0.0, 0.0]
        self.last_sent_cmd = [None, None] # ????????????????
        self.last_time = self.get_clock().now()
        self.odom_pub = self.create_publisher(Odometry, 'odom', 10)
        self.temp_pub = self.create_publisher(Float32, 'sensor/temperature', 10)
        self.humi_pub = self.create_publisher(Float32, 'sensor/humidity', 10)
        self.water_pub = self.create_publisher(Float32, 'sensor/water_level', 10)
        self.tf_broadcaster = TransformBroadcaster(self)
        # self.read_buffer = bytearray()
        self.buffer = bytearray()
        self.frame_queue = Queue()

        self.processor_thread = threading.Thread(target=self.frame_processing_loop)
        self.processor_thread.daemon = True
        self.processor_thread.start()

        self.create_subscription(Twist, 'cmd_vel', self.cmd_vel_callback, 10)
        # self.create_timer(0.02, self.send_velocity)

        self.linear_x = 0.0
        self.angular_z = 0.0

        self.create_timer(0.01, self.serial_read_timer_callback)
        self.create_timer(0.1, self.serial_write_timer_callback)
        # self.create_timer(0.01, self.frame_handler_timer_callback)

    def serial_init(self):
        try:
            self.ser = serial.Serial(self.port, baudrate=115200, timeout=0, write_timeout=0)
            self.ser.reset_input_buffer()
            self.get_logger().info(f"???????{self.port}")
        except Exception as e:
            self.get_logger().error(f"???????: {e}")
            raise

    def cmd_vel_callback(self, msg: Twist):
        self.linear_x = msg.linear.x
        self.angular_z = msg.angular.z
        wheel_base = 0.234
        v_l = self.linear_x - (self.angular_z * wheel_base / 2.0)
        v_r = self.linear_x + (self.angular_z * wheel_base / 2.0)
        self.last_cmd = [v_l, v_r]  # ???????
        # if [v_l, v_r] != getattr(self, 'last_cmd', [None, None]):# ????????????????????????????????
        #     self.last_cmd = [v_l, v_r]
        #     frame = self.build_frame(0x02, [v_l, v_r])
        #     try:
        #         self.ser.write(frame)
        #     except serial.SerialTimeoutException:
        #         self.get_logger().warn("????????????")
        #     except Exception as e:
        #         self.get_logger().error(f"?????: {e}")
        


    def build_frame(self, func_code, floats):
        frame = bytearray([0xAA, 0x55])
        data_len = 1 + len(floats) * 4 + 1
        frame.append(data_len)
        frame.append(func_code)
        for f in floats:
            frame.extend(struct.pack('<f', f))
        checksum = 0
        for b in frame[2:]:
            checksum ^= b
        frame.append(checksum)
        return frame

    def serial_write_timer_callback(self):
        v_l, v_r = self.last_cmd
        if [v_l, v_r] != self.last_sent_cmd:# ????????????????????????????????
            self.last_sent_cmd = [v_l, v_r]
            frame = self.build_frame(0x02, [v_l, v_r])
            try:
                self.ser.write(frame)
            except serial.SerialTimeoutException:
                self.get_logger().warn("????????????")
            except Exception as e:
                self.get_logger().error(f"?????: {e}")


    def serial_read_timer_callback(self):
        data = self.ser.read(self.ser.in_waiting or 1)
        if data:

            now = self.get_clock().now()
            if self.last_recv_time is not None:
                dt = (now - self.last_recv_time).nanoseconds / 1e6
                self.get_logger().info(f"? ??????: {dt:.1f} ms")
            self.last_recv_time = now

            self.buffer.extend(data)
            while True:
                head_idx = self.buffer.find(b'\xAA\x55')
                if head_idx == -1:
                    self.buffer.clear()
                    break
                if head_idx > 0:
                    self.buffer = self.buffer[head_idx:]
                if len(self.buffer) < 3:
                    break
                length = self.buffer[2]
                total_len = length + 3
                if len(self.buffer) < total_len:
                    break
                frame = self.buffer[:total_len]
                self.buffer = self.buffer[total_len:]

                checksum = 0
                for b in frame[2:-1]:
                    checksum ^= b
                if checksum == frame[-1]:
                    func_code = frame[3]
                    data_bytes = frame[4:-1]
                    self.frame_queue.put((func_code, data_bytes))  # ? ??
                    # self.handle_frame(func_code, data_bytes)  # ? ???????
                else:
                    self.get_logger().warn("????????")

    def frame_processing_loop(self):
        while rclpy.ok():
            try:
                func_code, data_bytes = self.frame_queue.get(timeout=0.1)
                self.handle_frame(func_code, data_bytes)
            except Exception:
                continue

    def handle_frame(self, func_code, data_bytes):
        # now = self.get_clock().now()
        # if self.last_recv_time is not None:
        #     dt = (now - self.last_recv_time).nanoseconds / 1e6
        #     # self.get_logger().info(f"? ??????: {dt:.1f} ms")
        # self.last_recv_time = now
        if len(data_bytes) % 4 != 0:
            self.get_logger().warn("??????float????")
            return
        floats = [struct.unpack('<f', data_bytes[i:i+4])[0] for i in range(0, len(data_bytes), 4)]
        # self.get_logger().info(f"???: 0x{func_code:02X}, ??: {floats}")

        if func_code == 0x01:
            floats = [struct.unpack('<f', data_bytes[i:i+4])[0] for i in range(0, len(data_bytes), 4)]
            if len(floats) >= 5:
                left, right, temp, humi, water = floats[:5]
                self.get_logger().info(
                    f"????????? - ??: {left:.3f} m/s, ??: {right:.3f} m/s, ??: {temp:.3f} ?, "
                    f"??: {humi:.3f}s %, ??: {water:.3f}"
                )
                self.temp_pub.publish(Float32(data=temp))
                self.humi_pub.publish(Float32(data=humi))
                self.water_pub.publish(Float32(data=water))
                self.update_odometry(left, right)

    def update_odometry(self, v_l, v_r):
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

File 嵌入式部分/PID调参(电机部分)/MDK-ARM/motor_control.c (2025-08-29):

#include "motor_control.h"
#include "tim.h"
//#include "usart.h"
#include "gpio.h"
#include <stdio.h>
#include <math.h>
#include "pid.h"

PID_HandleTypeDef pid_a;
PID_HandleTypeDef pid_b;

// 上一次编码器计数值
static int16_t last_count_a = 0;
static int16_t last_count_b = 0;

// 当前速度(脉冲数/100ms)
int16_t speed_a = 0;
int16_t speed_b = 0;

// 滤波后的速度
float filtered_speed_a = 0;
float filtered_speed_b = 0;

#define WHEEL_DIAMETER       0.065f
#define WHEEL_CIRCUMFERENCE  (3.1416f * WHEEL_DIAMETER) // ≈ 0.2042
#define GEAR_RATIO           30.0f
#define ENCODER_RESOLUTION   13.0f
#define QUADRATURE_MULTIPLIER 4.0f
#define INTERVAL_SEC         0.1f


// 滤波系数
static float alpha = 0.5f;

static int16_t GetDeltaCount(int16_t current, int16_t last)
{
    int16_t delta = current - last;
    if(delta > 32767) delta -= 65536;
    else if(delta < -32768) delta += 65536;
    return delta;
}

void Motor_Init(void)
{
    HAL_TIM_PWM_Start(&htim2, TIM_CHANNEL_3);  // Motor A
    HAL_TIM_PWM_Start(&htim2, TIM_CHANNEL_4);  // Motor B
    HAL_TIM_Encoder_Start(&htim3, TIM_CHANNEL_ALL);    // 编码器A
    HAL_TIM_Encoder_Start(&htim4, TIM_CHANNEL_ALL);    // 编码器B
    HAL_GPIO_WritePin(GPIOB, GPIO_PIN_2, GPIO_PIN_SET);  // STBY = 1

    last_count_a = (int16_t)__HAL_TIM_GET_COUNTER(&htim3);
    last_count_b = (int16_t)__HAL_TIM_GET_COUNTER(&htim4);
	
	PID_Init(&pid_a, 800.0f, 120.0f, 100.0f);
    PID_Init(&pid_b, 800.0f, 120.0f, 100.0f);
}

void Motor_UpdateSpeed(void)
{
    int16_t count_a = (int16_t)__HAL_TIM_GET_COUNTER(&htim3);
    int16_t count_b = (int16_t)__HAL_TIM_GET_COUNTER(&htim4);

    speed_a = GetDeltaCount(count_a, last_count_a);
    speed_b = GetDeltaCount(count_b, last_count_b);

    last_count_a = count_a;
    last_count_b = count_b;

	speed_a = -speed_a;
	
//    // 限幅防止跳变过大
//    if(speed_a > 300) speed_a = 300;
//    else if(speed_a < -300) speed_a = -300;

//    if(speed_b > 300) speed_b = 300;
//    else if(speed_b < -300) speed_b = -300;

    // 低通滤波
    filtered_speed_a = alpha * speed_a + (1 - alpha) * filtered_speed_a;
    filtered_speed_b = alpha * speed_b + (1 - alpha) * filtered_speed_b;

    static int print_cnt = 0;
    if(++print_cnt >= 10)
    {
        // printf("Raw Speed A=%d, B=%d | Filtered Speed A=%.2f, B=%.2f\r\n", speed_a, speed_b, filtered_speed_a, filtered_speed_b);
        print_cnt = 0;
    }
}


void Motor_Set(int16_t pwm_a, int16_t pwm_b, uint8_t dir_a, uint8_t dir_b)
{
	// 设置方向
	HAL_GPIO_WritePin(GPIOD, GPIO_PIN_0, dir_a ? GPIO_PIN_SET : GPIO_PIN_RESET); // AIN1
	HAL_GPIO_WritePin(GPIOD, GPIO_PIN_1, dir_a ? GPIO_PIN_RESET : GPIO_PIN_SET); // AIN2
	HAL_GPIO_WritePin(GPIOD, GPIO_PIN_2, dir_b ? GPIO_PIN_SET : GPIO_PIN_RESET); // BIN1
	HAL_GPIO_WritePin(GPIOD, GPIO_PIN_3, dir_b ? GPIO_PIN_RESET : GPIO_PIN_SET); // BIN2
	
	// 设置PWM占空比
	__HAL_TIM_SET_COMPARE(&htim2, TIM_CHANNEL_3, pwm_a); // 电机A
    __HAL_TIM_SET_COMPARE(&htim2, TIM_CHANNEL_4, pwm_b); // 电机B
}

//  

float Motor_ConvertToSpeed(float pulses)
{
    float pulses_per_rev = ENCODER_RESOLUTION * GEAR_RATIO * QUADRATURE_MULTIPLIER;
    float revolutions = pulses / pulses_per_rev;
    float distance = revolutions * WHEEL_CIRCUMFERENCE;
    float velocity = distance / INTERVAL_SEC;

    // 打印中间变量，调试用
//    printf("[DEBUG] pulses=%.2f, rev=%.5f, dist=%.5f, v=%.5f m/s\r\n",
//           pulses, revolutions, distance, velocity);

    return velocity;
}

float Motor_GetFilteredSpeedA(void)
{
    return Motor_ConvertToSpeed(filtered_speed_a);
}

float Motor_GetFilteredSpeedB(void)
{
    return Motor_ConvertToSpeed(filtered_speed_b);
}

// 速度的开环控制
int SpeedToPWM(float speed_mps)
{
    const float K = 750.0f;  // 估计值，调整试试
    float abs_speed = fabs(speed_mps);
    int pwm = (int)(abs_speed * K);

    if (pwm > 1000) pwm = 1000;
    if (pwm < 0) pwm = 0;

//    printf("[DEBUG] speed=%.5f, abs_speed=%.5f, pwm=%d\n", speed_mps, abs_speed, pwm);

    return pwm;
}

void Motor_SetTargetSpeed(float left_mps, float right_mps)
{
    pid_a.target = left_mps;
    pid_b.target = right_mps;

    // 当目标速度接近0时，强制清零积分，防止积分风暴导致停不下来
    if (fabs(left_mps) < 0.01f) {
        pid_a.integral = 0.0f;
        pid_a.prev_error = 0.0f;  // 也建议清理前次误差，避免积分抖动
    }
    if (fabs(right_mps) < 0.01f) {
        pid_b.integral = 0.0f;
        pid_b.prev_error = 0.0f;
    }
}

void Motor_PIDUpdate(void)
{
    float currentL = Motor_GetFilteredSpeedA();
    float currentR = Motor_GetFilteredSpeedB();

    float outputL_speed = PID_Calc(&pid_a, currentL);  // 目标速度 (±)
    float outputR_speed = PID_Calc(&pid_b, currentR);  // 目标速度 (±)

    int dirL = outputL_speed >= 0 ? 1 : 0;
    int dirR = outputR_speed >= 0 ? 1 : 0;

    // ⛳️ 速度转 PWM，使用绝对值
    int pwmL = SpeedToPWM(fabs(outputL_speed));
    int pwmR = SpeedToPWM(fabs(outputR_speed));

    // 限幅，防炸机
    if (pwmL > 1000) pwmL = 1000;
    if (pwmR > 1000) pwmR = 1000;

    Motor_Set(pwmL, pwmR, dirL, dirR);

    // 打印调试信息
    printf("Target L=%.2f R=%.2f | Real L=%.2f R=%.2f | PWM=%d %d DIR=%d %d\r\n",
           pid_a.target, pid_b.target, currentL, currentR, pwmL, pwmR, dirL, dirR);
}



void Motor_SetPWM(float pwm_left, float pwm_right)
{
    // 目标速度为0时，强制输出0
    if (fabsf(pwm_left) < 0.01f) pwm_left = 0.0f;
    if (fabsf(pwm_right) < 0.01f) pwm_right = 0.0f;

    int dirL = pwm_left >= 0 ? 1 : 0;
    int dirR = pwm_right >= 0 ? 1 : 0;

    int pwmL = (int)fabsf(pwm_left);
    int pwmR = (int)fabsf(pwm_right);

    if (pwmL > 1000) pwmL = 1000;
    if (pwmR > 1000) pwmR = 1000;

    // 如果都为0，考虑断电或STBY低电平
    if (pwmL == 0 && pwmR == 0) {
        // HAL_GPIO_WritePin(GPIOB, GPIO_PIN_2, GPIO_PIN_RESET); // 休眠电机，视具体硬件
    } else {
        // HAL_GPIO_WritePin(GPIOB, GPIO_PIN_2, GPIO_PIN_SET);
    }

    Motor_Set(pwmL, pwmR, dirL, dirR);
}

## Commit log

2025-07-07 第一次提交
2025-07-07 节点加入一个通信，用于yolo识别后人物的中心点坐标
2025-07-18 相机pull
    上传相机节点封装包
2025-07-18 yolov5封装
    上传yolov5节点封装包
2025-08-19 STM32F407使用STM32CubeMX配置HAL库成功移植正点原子LCD V3
2025-08-19 STM32F407多传感器移植FreeRTOS以及电机正反转测速
2025-08-19 STM32F407ZGT6移植多个传感器以及测试
2025-08-19 嵌入式部分
2025-08-19 PCB文件
2025-08-20 新增导航部分
    [dipan.STL, huapeng.STL, robot.urdf.xacro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]
2025-08-20 新增内容描述
2025-08-21 修复daohang
2025-08-21 Update README.md
    增加视觉部分的readme描述
2025-08-22 在main分支添加硬件清单.excel
    [硬件清单.xlsx]
2025-08-22 提交视觉和语音交互部分的遇到问题及解决方法
2025-08-25 增加了从模型广场下载模型的方法
2025-08-25 新增模型广场下载模型的方法
2025-08-28 嵌入式部分电机驱动程序
2025-08-28 传感器整合调通
2025-08-29 电机驱动部分，带PID控制速度
2025-08-29 更新freertos内容，与操作步骤一致

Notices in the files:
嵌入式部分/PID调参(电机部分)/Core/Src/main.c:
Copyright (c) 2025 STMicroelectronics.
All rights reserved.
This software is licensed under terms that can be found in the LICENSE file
